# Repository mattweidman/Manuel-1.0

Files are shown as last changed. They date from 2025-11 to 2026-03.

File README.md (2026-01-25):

# Manuel 1.0: Open-source robotic arm

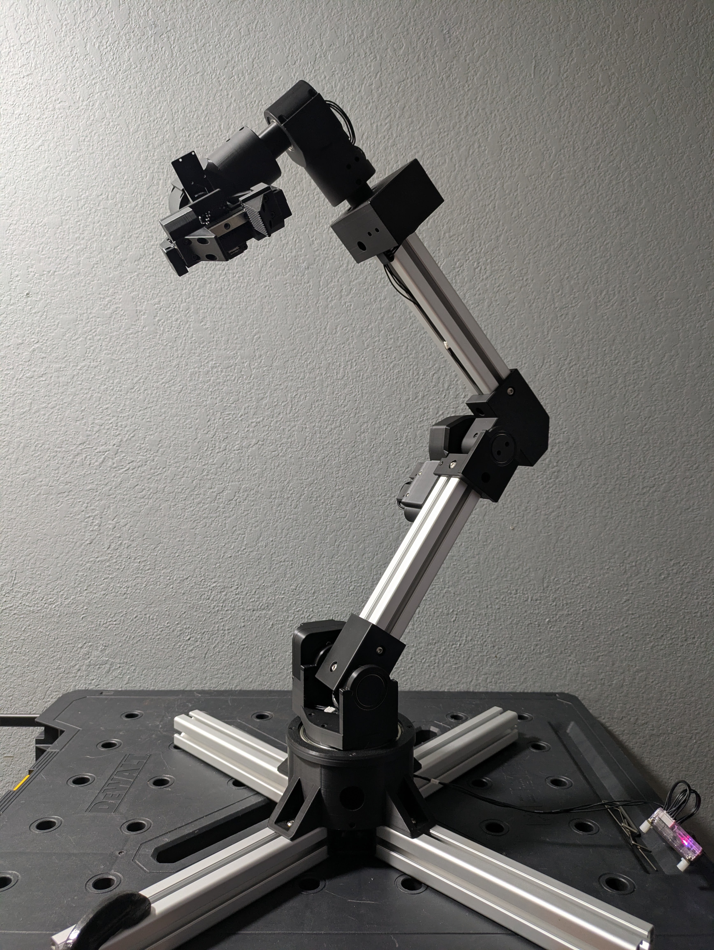
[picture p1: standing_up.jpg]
Robot arm standing up


Video: https://www.youtube.com/watch?v=q0eZf5LdW8s

This is an open-source robotic arm I made as a hobby project. It's flexible,
similar in size to a human arm, and relatively inexpensive. Besides a 3D
printer and a computer, no expensive tools (>$50) are required to build it.
Feel free to build and use this robot however you like, as long as it's safe.
I sincerely hope that someone besides me can find some use or enjoyment out of
this project.

Features:
* This robot is substantially cheaper than all commercial robotic arms (that I
know of) with similar size and torque capabilities.
* This arm is made entirely with 3D-printed components and mass-produced
parts you can find online. If you have a 3D printer, some cheap hobby tools,
and money for parts, you can build it.
* There are 7 motors: 6 degrees of freedom + a gripper.
* 4 out of 6 joints (waist + 3 wrist joints) can turn more than 360 degrees.
* Wrist joints allow the gripper to rotate completely in all 3 axes when
unobstructed. The gripper can point forward, backward, up, down, left, right,
and anywhere inbetween only by moving the wrist.
* The arm as I designed it reaches 860 mm from shoulder to gripper tip. That's
similar in length to a human arm. You can change the length by using shorter or
longer T-slot extrusions (mine are 300 mm each). A shorter arm will vibrate
less or be able to lift more.
* Using the length that I used, the arm can hold a 1 kg payload when extended.
* All motors are from the [Dynamixel X](https://www.robotis.us/x-series/)
series from Robotis. Robotis has excellent documentation and code resources,
so it is fairly straightforward to control the joints with any of their
[SDKs](https://github.com/ROBOTIS-GIT/DynamixelSDK) written in Python, C++,
Java, C#, and more. Linux, Windows, and Mac are all supported, and you can
connect the robot to a computer with USB.
* All motors are backdrivable.
* All 3D-printed components can be printed with standard PLA filament. For many
3D printers such as my Bambu Lab A1, no supports are needed.
* All components can be removed and replaced. No glue is used anywhere. Most
plastic components are connected with M3 screws and heat set inserts.
* Cables are well organized. If you follow the recommended cable lengths, you
shouldn't have any annoying dangling wires. Of course you will have to adjust
the cable lengths if you choose extrusions that are not 300 mm.

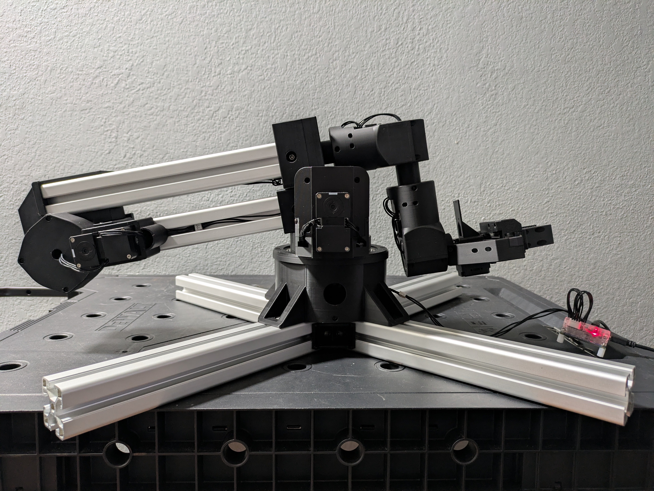
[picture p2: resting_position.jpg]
Robot arm in resting position


## Tips

* I recommend putting a maximum acceleration of "10" on all motors using the
[profile acceleration](https://emanual.robotis.com/docs/en/dxl/x/xl430-w250/#profile-acceleration)
setting. Acceleration that is too high will cause joints to vibrate, and you
won't get good accuracy. You can later adjust this as you see fit.
* I use 0.2mm Standard 3D printer settings for all parts except for the gears.
For the gears, I increase the wall loops to 4 to try to fill all of the teeth
completely.
* Some of the printed components have a small overhang inside the screw hole
where the screw meets the plastic. My printer can do some overhangs, but often
it leaves plastic threads sticking around, and the hole is often too small. You
can fix this by taking a small allen wrench and forcing it through the hole.
Then take a bigger one and do it again. Eventually you'll be able to fit the
screw in there.

## Tools needed

* Any computer with a USB port
* 3D printer that can print PLA; bed size should be at least 17 cm x 17 cm
* Soldering iron
* Crimping tool that can crimp
[JST SEH-001T-P0.6](https://emanual.robotis.com/docs/en/dxl/x/xl430-w250/#connector-information)
* Wire stripper
* 2mm Phillips screwdriver
* Hex drivers / allen wrenches, sizes 1.5mm, 2.0mm, 2.5mm, and 4mm
* Pliers
* Flathead screwdriver
* Table clamps

## Bill of materials

Item | Minimum needed | Bundle price | Total price
-|-|-|-
Motors and electronics
[DYNAMIXEL XM540-W270-T](https://www.robotis.us/dynamixel-xm540-w270-t/) | 2 | $482.89 | $965.78
[DYNAMIXEL XM430-W350-T](https://www.robotis.us/dynamixel-xm430-w350-t/) | 3 | $310.39 | $931.17
[DYNAMIXEL XL430-W250-T](https://www.robotis.us/dynamixel-xl430-w250-t/) | 2 | $27.50 | $55.00
[DYNAMIXEL starter set including U2D2 USB converter](https://robotis.us/dynamixel-starter-set-us/) | 1 | $68.66 | $68.66
Bearings and rails
[95x120x13mm bearing](https://www.amazon.com/dp/B0DD4B5DLV?ref=ppx_yo2ov_dt_b_fed_asin_title&th=1) | 1 | $16.99 | $16.99
[30x42x7mm bearings](https://www.amazon.com/dp/B082PXK5K9?ref=ppx_yo2ov_dt_b_fed_asin_title&th=1) | 10 | $15.19 / 10 | $15.19
[17x23x4mm bearings](https://www.amazon.com/dp/B0CRBBMTXD?ref=ppx_yo2ov_dt_b_fed_asin_title&th=1) | 4 | $13.29 / 10 | $13.29
[100mm linear rail with carriage](https://www.amazon.com/dp/B09SD9GXVP?ref=ppx_yo2ov_dt_b_fed_asin_title&th=1) | 1 | $16.89 | $16.89
[MGN9C carriage block](https://www.amazon.com/dp/B085NSZD14?ref=ppx_yo2ov_dt_b_fed_asin_title&th=1) | 1 | $13.99 | $13.99
Fasteners
[M3x6mm heat set inserts](https://www.amazon.com/dp/B0DG8R9DNX?ref=ppx_yo2ov_dt_b_fed_asin_title&th=1) | 81 | $7.99 / 140 | $7.99
[M3x5mm screws](https://www.amazon.com/dp/B08B1T4HHP?ref=ppx_yo2ov_dt_b_fed_asin_title&th=1) | 89 | $7.86 / 100 | $7.86
[M3x7mm screws](https://www.amazon.com/uxcell-M3x7mm-Thread-Button-Socket/dp/B01B1OD5Q4?th=1) | 4 | $7.99 / 100 | $7.99
[M3 hex nuts](https://www.amazon.com/Toms-world-100pcs-Stainless-Hexagon/dp/B0CMCKVB62) | 4 | $4.29 / 100 | $4.29
[M6 screws](https://www.amazon.com/dp/B07H16MXW9?ref=ppx_yo2ov_dt_b_fed_asin_title&th=1) | 26 | $10.99 / 50 | $10.99
[M6 T nuts](https://www.amazon.com/dp/B08DRBTXVG?ref=ppx_yo2ov_dt_b_fed_asin_title&th=1) | 26 | $15.09 / 50 | $15.09
Structure
[300mm 4040 T slot aluminum extrusions](https://www.amazon.com/dp/B0CP1YY3W8?ref=ppx_yo2ov_dt_b_fed_asin_title&th=1) | 6 | $33.99 / 4 | $67.98 
[90&deg; M6 T slot extrusion connector](https://www.amazon.com/dp/B0BS6HPXKL?ref=ppx_yo2ov_dt_b_fed_asin_title&th=1) | 4 | $23.99 / 24 | $23.99
Wiring
[22 gauge wire](https://www.amazon.com/dp/B01K4RP8PU?ref=ppx_yo2ov_dt_b_fed_asin_title) | 160 cm | $12.48 / 100 ft | $12.48
[JST EHR-03 (female JST-EH)](https://www.digikey.com/en/products/detail/jst-sales-america-inc/EHR-3/527225) | 12 | $0.048 | $0.58
[JST SEH-001T-P0.6 (JST-EH socket contact)](https://www.digikey.com/en/products/detail/jst-sales-america-inc/SEH-001T-P0-6/26213194) | 36 | $2.52 / 100 | $2.52
[SMP-03V-BC (female JST-SM)](https://www.digikey.com/en/products/detail/jst-sales-america-inc/SMP-03V-BC/2514249) | 4 | $0.10 | $0.40
[SMR-03V-B (male JST-SM)](https://www.digikey.com/en/products/detail/jst-sales-america-inc/SMR-03V-B/5702345) | 4 | $0.10 | $0.40
[SHF-001T-0.8BS (JST-SM socket contact)](https://www.digikey.com/en/products/detail/jst-sales-america-inc/SHF-001T-0-8BS/26741597) | 12 | $3.73 / 100 | $3.73
[SYM-001T-P0.6 (JST-SM pin contact)](https://www.digikey.com/en/products/detail/jst-sales-america-inc/SYM-001T-P0-6-N/26213081) | 12 | $8.21 / 100 | $8.21
Filament
[PLA filament](https://www.amazon.com/Printer-Filament-SUNLU-Dimensional-Accuracy/dp/B07XG3RM58) | 1.14 kg | $13.99 / kg | $27.98
Grease
[Multi-Purpose Synthetic Grease](https://www.amazon.com/dp/B000XBH9HI) | Optional | $10.28 / 3 oz | $10.28
**Total** | | | **$2,309.72**

Taxes and shipping are not included. These prices will vary depending on where
you live.

For any JST components, I recommend you get at least double the minimum indicated
above. They are only a few cents apiece, and they are very easy to mess up if you
don't have much experience crimping.

## Cable lengths

Here is a list of all electronics and the lengths of cables between them, from
base to tip. Every cable is written of the form "X-N-X", where "N" indicates
the cable length in cm, and "X" indicates the type of connector:

* FEH: Female JST EH (JST EHR-03)
* FSM: Female JST-SM (SMP-03V-BC)
* MSM: Male JST-SM (SMR-03V-B)

Note that many Dynamixel motors come with an 18 cm female-female JST-EH cable
included, so if you see "FEH-18-FEH" in the list, you don't need to make it yourself.

All cables consist of 3 wires. All F/M connectors are
[3-pin JST EH connectors](https://emanual.robotis.com/docs/en/dxl/x/xl430-w250/#connector-information).

1. [U2D2](https://emanual.robotis.com/docs/en/parts/interface/u2d2/) USB
connector
1. FEH-18-FSM
1. MSM-10-FEH
1. [XM430-W350-T](https://emanual.robotis.com/docs/en/dxl/x/xm430-w350/)
(waist)
1. FEH-13-MSM
1. FSM-12-FEH
1. [XM540-W270-T](https://emanual.robotis.com/docs/en/dxl/x/xm540-w270/)
(shoulder)
1. FEH-40-FSM (change length if you used a different extrusion length)
1. MSM-17-FEH
1. [XM540-W270-T](https://emanual.robotis.com/docs/en/dxl/x/xm540-w270/)
(elbow)
1. FEH-32-MSM
1. FSM-18-FEH (change length if you used a different extrusion length)
1. [XM430-W350-T](https://emanual.robotis.com/docs/en/dxl/x/xm430-w350/)
(wrist 1)
1. FEH-18-FEH
1. [XM430-W350-T](https://emanual.robotis.com/docs/en/dxl/x/xm430-w350/)
(wrist 2)
1. FEH-21-FEH
1. [XL430-W350-T](https://emanual.robotis.com/docs/en/dxl/x/xl430-w250/)
(wrist 3)
1. FEH-15-FEH
1. [XL430-W350-T](https://emanual.robotis.com/docs/en/dxl/x/xl430-w250/)
(gripper)

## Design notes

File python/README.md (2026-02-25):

# Sample Python code

This directory contains sample code you can use to control the Manuel 1.0 robot
arm.

Files:
* manuel1.py: Common functions and classes for use in the samples
* get_positions.py: Script that retrieves all joint positions from the robot,
including the ability to freeze or unfreeze the arm on a timer
* wave.py: Robot arm waves its gripper like in a greeting
* config.json: Contains saveable values, including the USB port, baud rate, and
origin joint position

## Setup

1. Make sure you have dynamixel_sdk installed: `pip install dynamixel-sdk`
2. Connect the U2D2 USB converter module to the robot, to a power outlet, and
to your computer. Flip the switch on.
3. In `config.json`, set `usb_port` to the name of the USB port that the U2D2
module is connected to.
4. Make sure no other applications on your computer are connected to the robot.
If the Dynamixel Wizard is connected, either click the disconnect button or
close the program.
5. Move the robot into resting position, where the wrist lies flat on the
shoulder. This will be your "origin position", which all other positions
will be relative to.
6. Save the origin position in `config.json` with
`python3 "python/get_positions.py -s`
7. You're ready to start developing. For an example, try out the code in
`wave.py` with `python3 "python/wave.py`. Make sure the robot has a clear space
around it before running.

## get_positions.py

`get_positions.py` is a useful script you can use to get the joint positions.
You can set a timer to give you time to manually move it into a certain
position before the joint positions are recorded. You can also use it to
freeze or unfreeze all joints on a timer.

### Parameters

#### --delay_to_unfreeze

If the robot is currently frozen (torque enabled in all joints), the robot will
unfreeze (disable all of its joints) after the specified number of seconds.
This is useful if you want to disable the robot, and you want to give yourself
time to grab it to keep it from falling.

Syntax:

`python3 "python/get_positions.py -delay_to_unfreeze <float>`

`python3 "python/get_positions.py -du <float>`

Example:

`"python/get_positions.py -du 4.5`

#### --delay_to_record

Positions will not be recorded until the specified number of seconds have
lapsed. This time begins after the time in `--delay_to_unfreeze` completes.
This is useful if you want to record the position of a robot in a particular
position, but you need time to get move from your computer to the robot before
you manually manipulate it. Sort of like setting a timer on your camera.

Syntax:

`python3 "python/get_positions.py --delay_to_record <float>`

`python3 "python/get_positions.py -dr <float>`

Example:

`"python/get_positions.py -dr 4.5`

#### --freeze

Whether the robot should freeze when it records. You might want to do this if
you want to let go of the robot after recording its position, but you don't
want it to fall yet.

Syntax:

`python3 "python/get_positions.py --freeze`

`python3 "python/get_positions.py -f`

#### --save

When this flag is used, the robot will save its position in the
`origin_positions` JSON property of `config.json`.

Syntax:

`python3 "python/get_positions.py --save`

`python3 "python/get_positions.py -s`

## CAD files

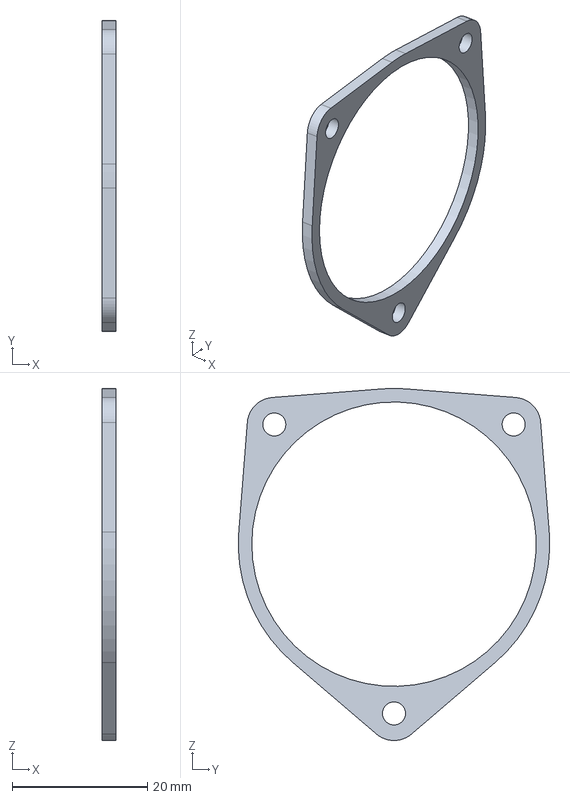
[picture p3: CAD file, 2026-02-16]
models/step/elbow/large_bearing_cap.step
2.00 x 46.0 x 52.0 mm

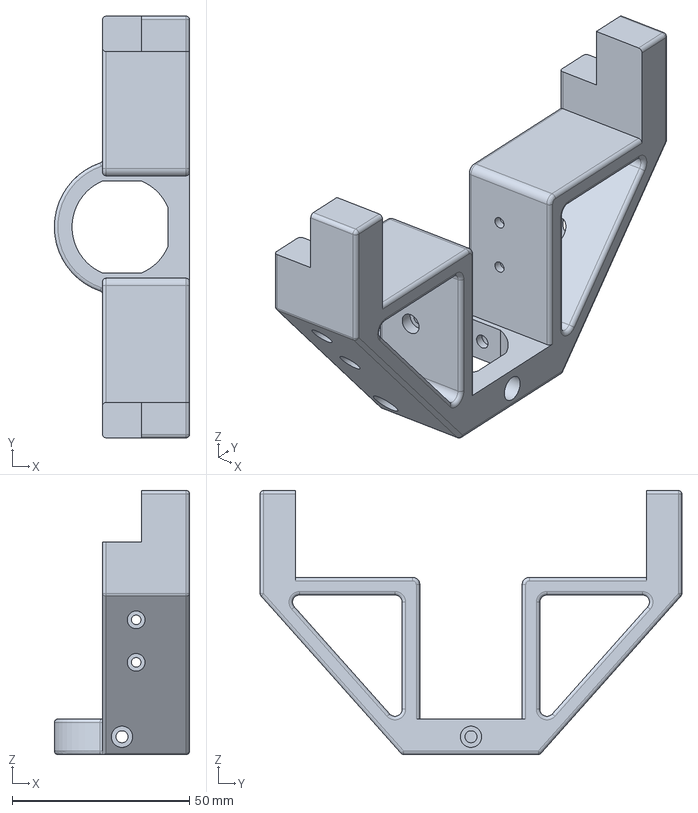
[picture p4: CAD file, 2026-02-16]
models/step/gripper/chassis.step
38.2 x 119.0 x 74.5 mm

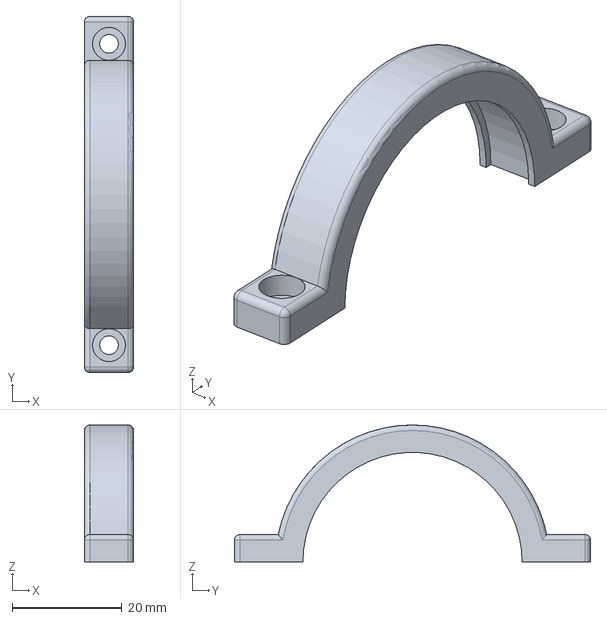
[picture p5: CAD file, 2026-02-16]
models/step/shoulder/idle_bearing_cap.step
9.00 x 65.0 x 25.0 mm

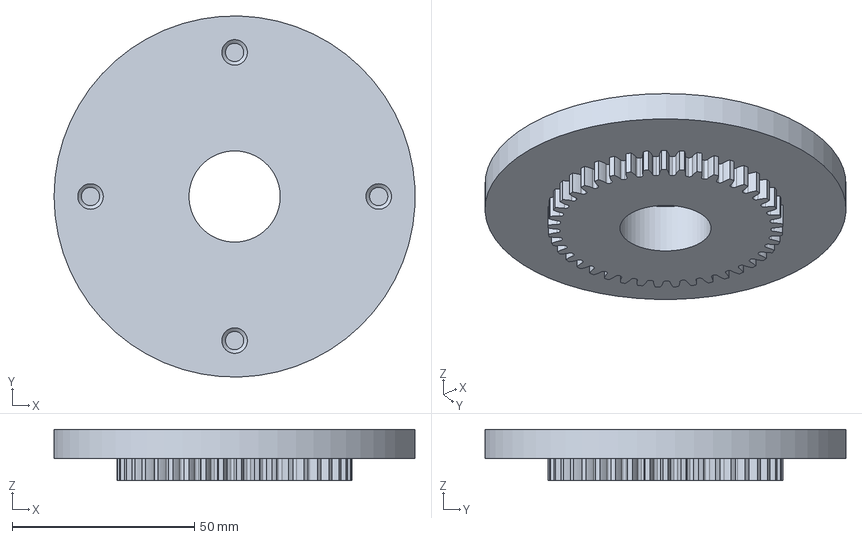
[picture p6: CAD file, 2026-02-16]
models/step/waist/output_gear.step
98.9 x 99.0 x 14.0 mm

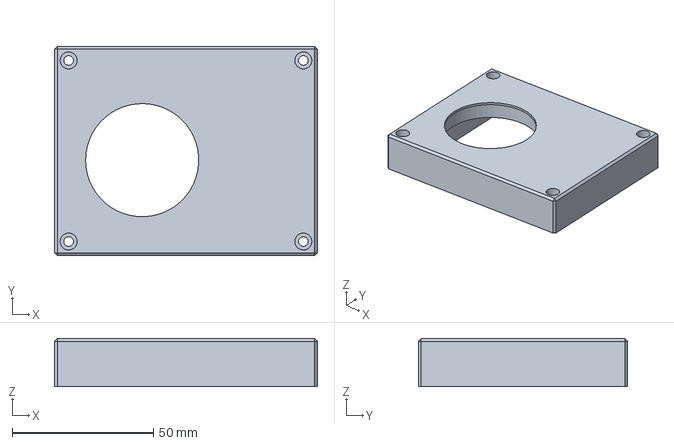
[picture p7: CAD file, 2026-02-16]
models/step/wrist_1/top_case.step
93.0 x 74.0 x 17.0 mm

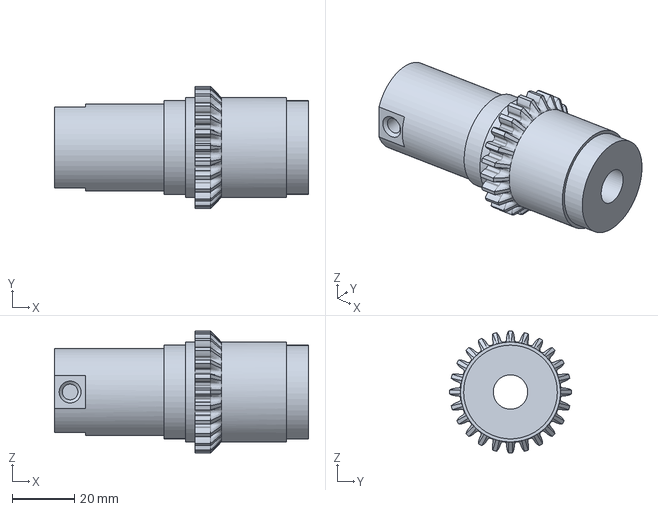
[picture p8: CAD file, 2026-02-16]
models/step/wrist_2/output_shaft.step
81.3 x 39.0 x 39.0 mm

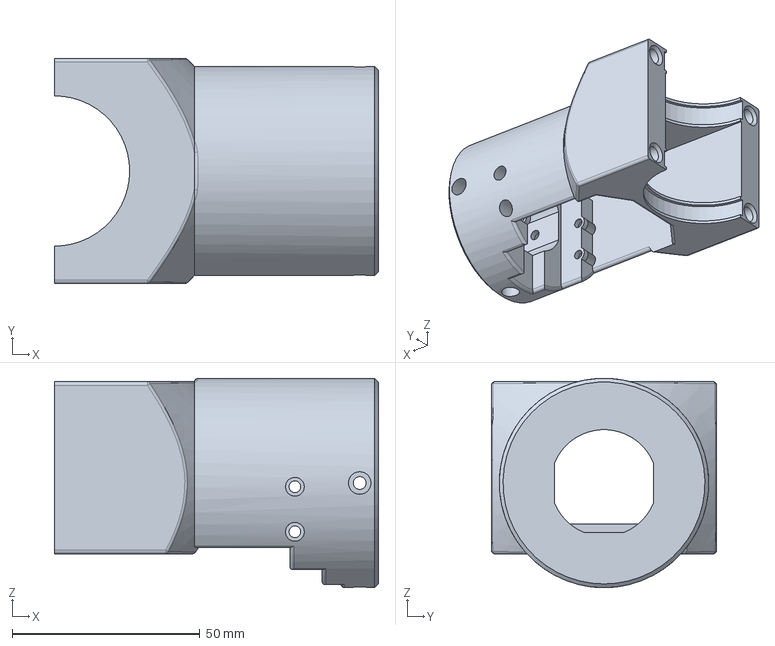
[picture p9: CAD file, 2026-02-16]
models/step/wrist_3/cylinder_gearbox.step
86.3 x 60.0 x 55.7 mm

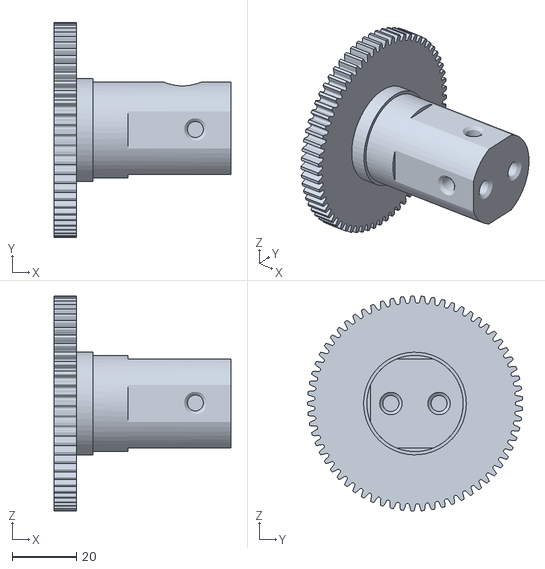
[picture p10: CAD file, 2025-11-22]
models/stl/elbow/big_gear.stl
55.0 x 67.0 x 67.0

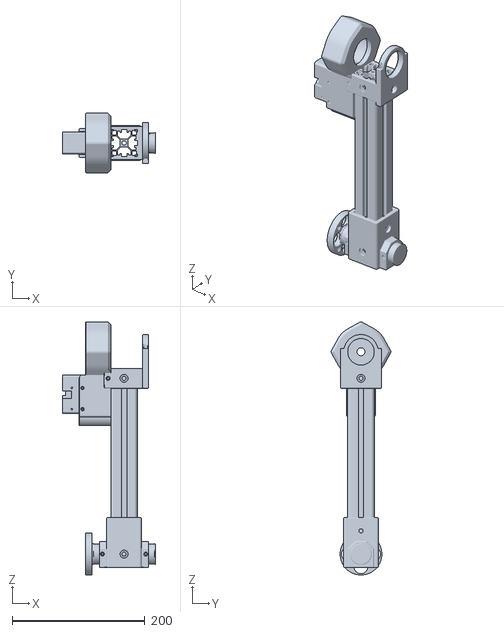
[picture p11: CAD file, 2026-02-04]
urdf/collision_links/upper_arm_collision.stl
139.8 x 89.9 x 381.4

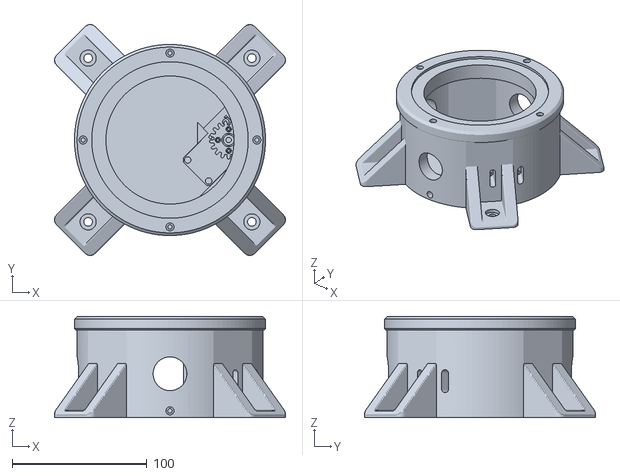
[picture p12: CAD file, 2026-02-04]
urdf/visual_links/base_visual.stl
171.2 x 171.2 x 75.0

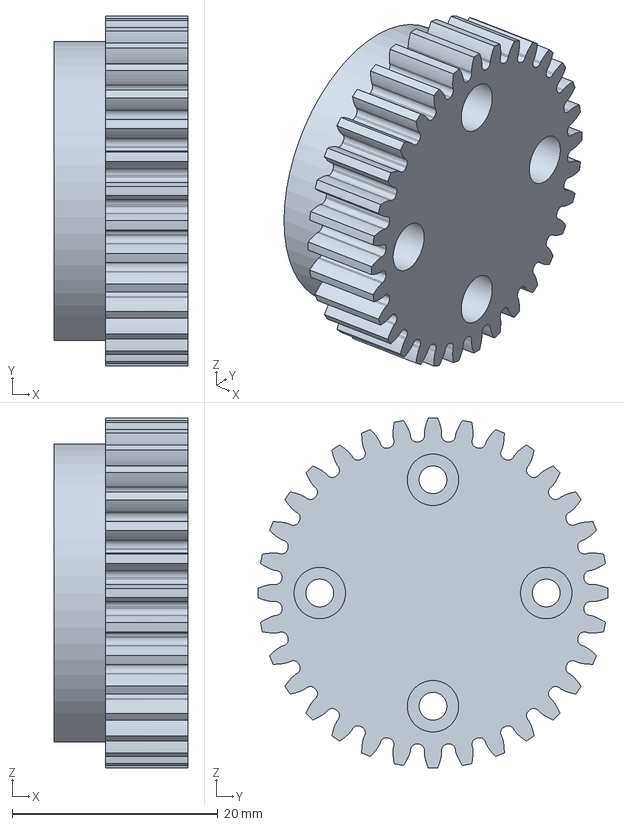
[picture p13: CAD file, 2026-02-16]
models/step/elbow/small_gear.step
13.0 x 34.0 x 34.0 mm

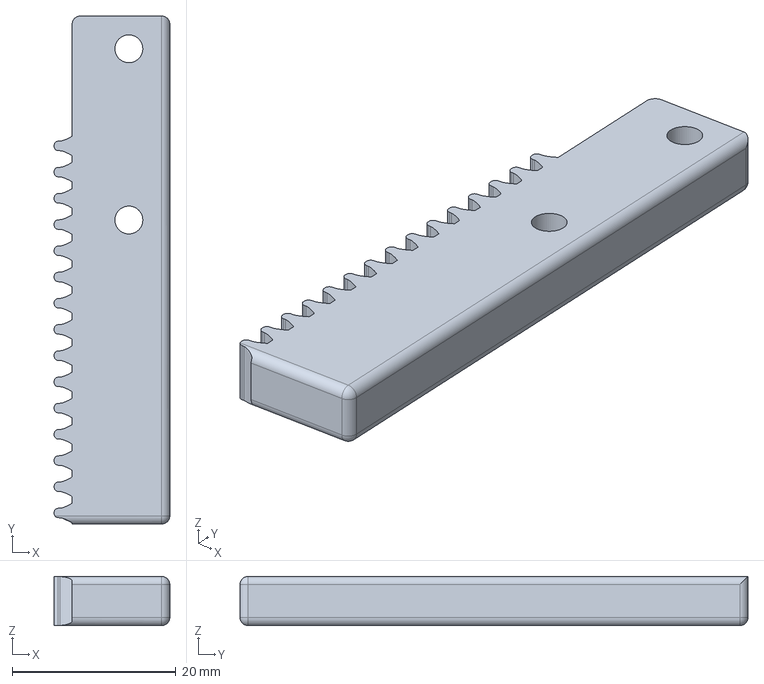
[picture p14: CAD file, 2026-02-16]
models/step/gripper/bottom_linear_gear.step
14.1 x 62.0 x 6.00 mm

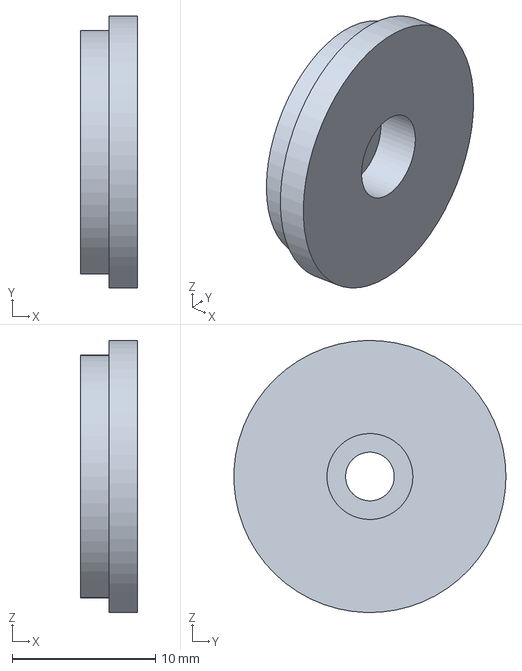
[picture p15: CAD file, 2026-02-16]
models/step/shoulder/planet_gear_cap_1of4.step
4.00 x 19.0 x 19.0 mm

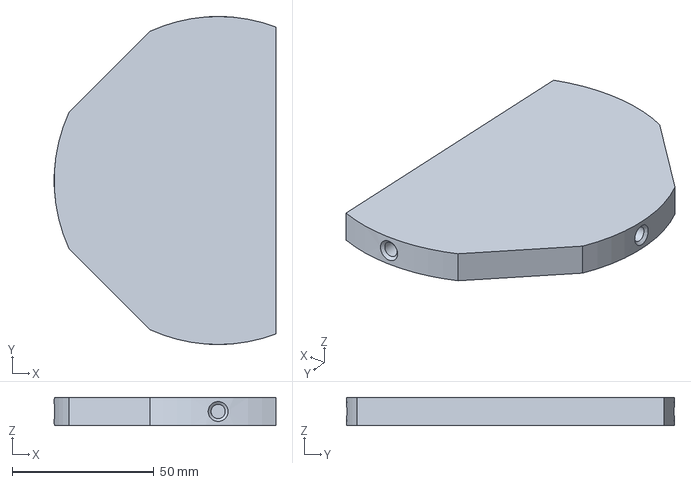
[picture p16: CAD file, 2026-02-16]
models/step/waist/floor.step
78.1 x 115.6 x 10.0 mm

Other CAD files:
models/step/wrist_1/shaft_gear.step
models/step/wrist_2/rotor_gear.step
models/step/wrist_3/output_shaft.step
urdf/collision_links/wrist_12_collision.stl
models/step/elbow/bearing_holder.step
models/step/elbow/bearing_holder_cap.step
models/step/elbow/box_cover.step
models/step/elbow/elbow_box.step
models/step/elbow/shaft_mount.step
models/step/elbow/shaft_spacer_1of2.step
models/step/elbow/shaft_stopper.step
models/step/gripper/camera_mount.step
models/step/gripper/carriage_mount_1of2.step
models/step/gripper/finger_1of2.step
models/step/gripper/left_rail_holder.step
models/step/gripper/right_rail_holder.step
models/step/gripper/rotor_gear.step
models/step/gripper/top_linear_gear.step
models/step/shoulder/box_side_bearing_cap.step
models/step/shoulder/carriage_back.step
models/step/shoulder/carriage_front.step
models/step/shoulder/extrusion_connector.step
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

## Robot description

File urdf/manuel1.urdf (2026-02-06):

<?xml version="1.0" ?>
<robot name="manuel1">

  <link name="base_link">
    <visual>
        <geometry>
            <mesh filename="visual_links/base_visual.stl" scale="0.001 0.001 0.001"/>
        </geometry>
    </visual>
    <collision>
        <geometry>
            <mesh filename="collision_links/base_collision.stl" scale="0.001 0.001 0.001"/>
        </geometry>
    </collision>
  </link>

  <joint name="waist_joint" type="revolute">
    <parent link="base_link"/>
    <child link="shoulder_link"/>
    <origin rpy="0.0 0.0 0.0" xyz="0.0 0.0 0"/>
    <axis xyz="0 0 1"/>
    <limit lower="-3.14159265" upper="3.14159265"/>
  </joint>

  <link name="shoulder_link">
    <visual>
        <geometry>
            <mesh filename="visual_links/shoulder_visual.stl" scale="0.001 0.001 0.001"/>
        </geometry>
    </visual>
    <collision>
        <geometry>
            <mesh filename="collision_links/shoulder_collision.stl" scale="0.001 0.001 0.001"/>
        </geometry>
    </collision>
  </link>

  <joint name="shoulder_joint" type="revolute">
    <parent link="shoulder_link"/>
    <child link="upper_arm_link"/>
    <origin rpy="0.0 0.0 0.0" xyz="0.0 0.0 0.1307"/>
    <axis xyz="1 0 0"/>
    <limit lower="-1.57079632" upper="1.57079632"/>
  </joint>

  <link name="upper_arm_link">
    <visual>
        <origin xyz="0 0 -0.1307" rpy="0 0 0" />
        <geometry>
            <mesh filename="visual_links/upper_arm_visual.stl" scale="0.001 0.001 0.001"/>
        </geometry>
    </visual>
    <collision>
        <origin xyz="0 0 -0.1307" rpy="0 0 0" />
        <geometry>
            <mesh filename="collision_links/upper_arm_collision.stl" scale="0.001 0.001 0.001"/>
        </geometry>
    </collision>
  </link>

  <joint name="elbow_joint" type="revolute">
    <parent link="upper_arm_link"/>
    <child link="forearm_link"/>
    <origin rpy="0.0 0.0 0.0" xyz="0.0 0.0 0.305"/>
    <axis xyz="1 0 0"/>
    <limit lower="0.0" upper="3.14159265"/>
  </joint>

  <link name="forearm_link">
    <visual>
        <origin xyz="0 0 -0.4357" rpy="0 0 0" />
        <geometry>
            <mesh filename="visual_links/forearm_visual.stl" scale="0.001 0.001 0.001"/>
        </geometry>
    </visual>
    <collision>
        <origin xyz="0 0 -0.4357" rpy="0 0 0" />
        <geometry>
            <mesh filename="collision_links/forearm_collision.stl" scale="0.001 0.001 0.001"/>
        </geometry>
    </collision>
  </link>

  <joint name="wrist_1_joint" type="revolute">
    <parent link="forearm_link"/>
    <child link="wrist_12_link"/>
    <origin rpy="0.0 0.0 0.0" xyz="0.0 0.06 0.0"/>
    <axis xyz="0 0 1"/>
    <limit lower="-3.14159265" upper="3.14159265"/>
  </joint>

  <link name="wrist_12_link">
    <visual>
        <origin xyz="0 -0.06 -0.4357" rpy="0 0 0" />
        <geometry>
            <mesh filename="visual_links/wrist_12_visual.stl" scale="0.001 0.001 0.001"/>
        </geometry>
    </visual>
    <collision>
        <origin xyz="0 -0.06 -0.4357" rpy="0 0 0" />
        <geometry>
            <mesh filename="collision_links/wrist_12_collision.stl" scale="0.001 0.001 0.001"/>
        </geometry>
    </collision>
  </link>

  <joint name="wrist_2_joint" type="revolute">
    <parent link="wrist_12_link"/>
    <child link="wrist_23_link"/>
    <origin rpy="0.0 0.0 0.0" xyz="0.0 0.0 0.4033"/>
    <axis xyz="1 0 0"/>
    <limit lower="-3.14159265" upper="3.14159265"/>
  </joint>

  <link name="wrist_23_link">
    <visual>
        <origin xyz="0 -0.06 -0.839" rpy="0 0 0" />
        <geometry>
            <mesh filename="visual_links/wrist_23_visual.stl" scale="0.001 0.001 0.001"/>
        </geometry>
    </visual>
    <collision>
        <origin xyz="0 -0.06 -0.839" rpy="0 0 0" />
        <geometry>
            <mesh filename="collision_links/wrist_23_collision.stl" scale="0.001 0.001 0.001"/>
        </geometry>
    </collision>
  </link>

  <joint name="wrist_3_joint" type="revolute">
    <parent link="wrist_23_link"/>
    <child link="gripper_link"/>
    <origin rpy="0.0 0.0 0.0" xyz="-0.1383 0.0 0.0"/>
    <axis xyz="0 0 1"/>
    <limit lower="-3.14159265" upper="3.14159265"/>
  </joint>

  <link name="gripper_link">
    <visual>
        <origin xyz="0.1383 -0.06 -0.839" rpy="0 0 0" />
        <geometry>
            <mesh filename="visual_links/gripper_visual.stl" scale="0.001 0.001 0.001"/>
        </geometry>
    </visual>
    <collision>
        <origin xyz="0.1383 -0.06 -0.839" rpy="0 0 0" />
        <geometry>
            <mesh filename="collision_links/gripper_collision.stl" scale="0.001 0.001 0.001"/>
        </geometry>
    </collision>
  </link>
</robot>

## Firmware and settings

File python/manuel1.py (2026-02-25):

# Common APIs to use in different control scripts for Manuel 1.0

import dynamixel_sdk
import json
from pathlib import Path
from time import sleep

scriptDirectory = Path(__file__).resolve().parent
with open(scriptDirectory/'config.json', 'r') as configFile:
    config = json.load(configFile)

usbPort = config['usb_port']
baudRate = config['baud_rate']
originPositions = config['origin_positions']

portHandler = dynamixel_sdk.PortHandler(usbPort)
packetHandler = dynamixel_sdk.PacketHandler(2.0)

# Open port
if portHandler.openPort():
    print("Succeeded to open the port")
else:
    print("Failed to open the port")
    quit()

# Set port baudrate
if portHandler.setBaudRate(baudRate):
    print("Succeeded to change the baudrate")
else:
    print("Failed to change the baudrate")
    quit()

# Throw an exception if a message failed in some way.
def handle_results(motor_id: int, address: int, comm_result: int, error):
    if comm_result == dynamixel_sdk.COMM_SUCCESS and error == 0:
        return

    details = f'''
Motor ID: {motor_id}
Address: {address}
Result = {comm_result}
Error = {error}
'''
    
    raise Exception("Message to motor failed. Details:" + details)

# Enable torque for a motor.
def enable_torque(motor_id: int, enable: bool = True):
    address = 64

    comm_result, error = packetHandler.write1ByteTxRx(
        portHandler,
        motor_id,
        address,
        data=1 if enable else 0)

    handle_results(motor_id, address, comm_result, error)
    print(f"Successfully {'enabled' if enable else 'disabled'} torque for motor {motor_id}.")

def is_torque_enabled(motor_id: int):
    '''Get whether torque is enabled for a motor.'''
    address = 64

    enabled, comm_result, error = packetHandler.read1ByteTxRx(
        portHandler,
        motor_id,
        address)
    
    handle_results(motor_id, address, comm_result, error)
    return False if enabled == 0 else True

def set_operating_mode(motor_id: int, mode: int):
    '''Set the operating mode for a motor.

    Modes:
    * 1: velocity control mode
    * 3: position control mode (default)
    * 4: extended position control mode
    * 16: PWM control mode
    '''
    address = 11

    comm_result, error = packetHandler.write1ByteTxRx(
        portHandler,
        motor_id,
        address,
        data=mode)

    handle_results(motor_id, address, comm_result, error)
    print(f"Set operating mode of motor {motor_id} to {mode}.")

def get_operating_mode(motor_id: int):
    '''Get the operating mode for a motor.

    Modes:
    * 1: velocity control mode
    * 3: position control mode (default)
    * 4: extended position control mode
    * 16: PWM control mode
    '''
    address = 11

    mode, comm_result, error = packetHandler.read1ByteTxRx(
        portHandler,
        motor_id,
        address)
    
    handle_results(motor_id, address, comm_result, error)
    return mode

# Read position of a motor.
def read_position(motor_id: int) -> int:
    address = 132

    position, comm_result, error = packetHandler.read4ByteTxRx(
        portHandler,
        motor_id,
        address)
    
    # Ensure that the upper half of integers are represented as negative
    if (position >= 2**31):
        position = position - 2**32
    
    handle_results(motor_id, address, comm_result, error)
    print(f"Position of motor {motor_id}: {position}")
    return position

# Write position of a motor.
def write_position(motor_id: int, target_position: int):
    address = 116

    comm_result, error = packetHandler.write4ByteTxRx(
        portHandler,
        motor_id,
        address,
        data=target_position)
    
    handle_results(motor_id, address, comm_result, error)
    print(f"Set goal position of motor {motor_id} to {target_position}.")

def read_pwm(motor_id: int):
    address = 124

    pwm, comm_result, error = packetHandler.read2ByteTxRx(
        portHandler,
        motor_id,
        address)
    
    # Ensure that the upper half of integers are represented as negative
    if (pwm >= 2**15):
        pwm = pwm - 2**16
    
    handle_results(motor_id, address, comm_result, error)
    print(f"PWM of motor {motor_id}: {pwm}")
    return pwm

def write_pwm(motor_id: int, target_pwm: int):
    '''Write PWM (torque) for a motor.'''
    address = 100

    comm_result, error = packetHandler.write2ByteTxRx(
        portHandler,
        motor_id,
        address,
        data=target_pwm)
    
    handle_results(motor_id, address, comm_result, error)
    print(f"Set goal PWM of motor {motor_id} to {target_pwm}.")

def set_velocity(motor_id: int, velocity: int):
    '''
    Setting this to 0 will choose the maximum velocity. The max value
    is 32,767, in units of 0.229 rev/min.
    '''
    address = 112

    comm_result, error = packetHandler.write4ByteTxRx(
        portHandler,
        motor_id,
        address,
        data=velocity)
    
    handle_results(motor_id, address, comm_result, error)
    print(f"Set the velocity of {motor_id} to {velocity}.")

def set_acceleration(motor_id: int, acceleration: int):
    '''
    Setting this to 0 will choose the maximum acceleration. The max value
    is 32,737, in units of 214.577 rev/min^2.
    '''
    address = 108

    comm_result, error = packetHandler.write4ByteTxRx(
        portHandler,
        motor_id,
        address,
        data=acceleration)
    
    handle_results(motor_id, address, comm_result, error)
    print(f"Set the acceleration of {motor_id} to {acceleration}.")

POSITION_CLOSENESS_THRESHOLD = 5
TICK_SECONDS = 0.01
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

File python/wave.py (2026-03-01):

from manuel1 import RobotConfig, originPositions

regular_velocities = [100, 150, 50, 100, 100, 100, 100]
waving_velocities = [150] * 7
regular_accelerations = [10] * 7
waving_accelerations = [20] * 7

robot_config = RobotConfig(motor_ids=[2, 3, 4, 5, 6, 7, 8])
robot_config.set_all_operating_modes_to_extended_position()
robot_config.set_velocities(regular_velocities)
robot_config.set_accelerations(regular_accelerations)
robot_config.enable_torque(True)

def arr_sum(arr1, arr2):
    return [x + y for x, y in zip(arr1, arr2)]

def move_to_relative_position(arr):
    pos = arr_sum(originPositions, arr)
    robot_config.write_positions_and_wait(pos)

wave_start = [-2115, 1742, 732, 800, -896, -1162]
wave_end = [-2115, 1742, 732, 1800, -896, -1162]

move_to_relative_position(wave_start)

robot_config.set_velocities(waving_velocities)
robot_config.set_accelerations(waving_accelerations)

move_to_relative_position(wave_end)
move_to_relative_position(wave_start)
move_to_relative_position(wave_end)
move_to_relative_position(wave_start)

robot_config.set_velocities(regular_velocities)
robot_config.set_accelerations(regular_accelerations)

move_to_relative_position([0, 0, 0, 0, 0, 0, 0])

robot_config.enable_torque(False)

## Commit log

2025-11-22 Document wire lengths
2025-11-22 STL files
    [bearing_cap.stl, bearing_holder.stl, bearing_holder_cap.stl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]
2025-11-23 Add elbow box component and minor changes to readme
    [elbow_box.stl]
2025-11-23 Bill of materials
2026-01-03 Add grease to BOM
2026-01-22 Change wires in waist
2026-01-25 Use JST-SM connectors in the middle of wires instead of JST-EH
2026-02-04 STL files for visuals and collisions of links
    [base_collision.stl, base_visual.stl, forearm_collision.stl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]
2026-02-04 Start base link urdf
    [manuel1.urdf]
2026-02-06 Set up collision; visualization works with URDF Visualizer VS code extension
    [manuel1.urdf]
2026-02-06 Shoulder joint
    [manuel1.urdf]
2026-02-06 Upper arm URDF
    [manuel1.urdf]
2026-02-06 Elbow joint and forearm
    [manuel1.urdf]
2026-02-06 Wrist 1 joint
    [manuel1.urdf]
2026-02-06 Wrist 2 joint
    [manuel1.urdf]
2026-02-06 Wrist 3 / gripper
    [manuel1.urdf]
2026-02-06 Change elbow and shoulder limits
    [manuel1.urdf]
2026-02-07 Move URDF directory to top level
    [base_collision.stl, base_visual.stl, forearm_collision.stl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]
2026-02-16 Step files
    [bearing_cap.step, bearing_holder.step, bearing_holder_cap.step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]
2026-02-25 Move from sample_code/python/ to python/
2026-03-01 Fixed some redundant code in wave.py
    [wave.py]
